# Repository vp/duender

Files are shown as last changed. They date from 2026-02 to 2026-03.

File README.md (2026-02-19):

<!-- Improved compatibility of back to top link: See: https://github.com/othneildrew/Best-README-Template/pull/73 -->

<!--
*** Thanks for checking out the Best-README-Template. If you have a suggestion
*** that would make this better, please fork the repo and create a pull request
*** or simply open an issue with the tag "enhancement".
*** Don't forget to give the project a star!
*** Thanks again! Now go create something AMAZING! :D
-->

<!-- PROJECT SHIELDS -->
<!--
*** I'm using markdown "reference style" links for readability.
*** Reference links are enclosed in brackets [ ] instead of parentheses ( ).
*** See the bottom of this document for the declaration of the reference variables
*** for contributors-url, forks-url, etc. This is an optional, concise syntax you may use.
*** https://www.markdownguide.org/basic-syntax/#reference-style-links
-->
<!--
[![Contributors][contributors-shield]][contributors-url]
[![Forks][forks-shield]][forks-url]
[![Stargazers][stars-shield]][stars-url]
[![Issues][issues-shield]][issues-url]
[![Unlicense License][license-shield]][license-url]
[![LinkedIn][linkedin-shield]][linkedin-url]
-->

<!-- PROJECT LOGO -->
<br />
<div align="center">
  <a href="https://www.printables.com/model/1300968-duender-mgn9h-2x-creality-ender-3-corexy-convertio">
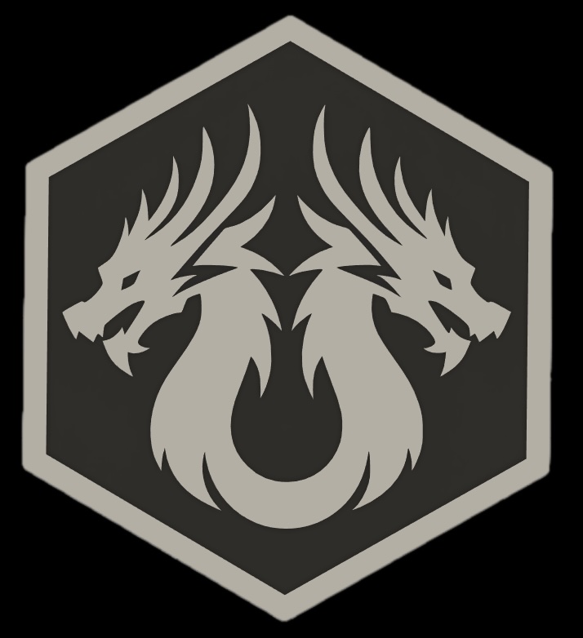
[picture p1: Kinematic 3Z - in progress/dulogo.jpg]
    
  </a>

  <h3 align="center">Duender mods, triple Z and more...</h3>
  <p align="center">
    Some thougths and mods for the duender project here.
    <br />Note: this is NOT an official repo, Irbis3D repo is <a href="https://github.com/Irbis3D">HERE</a>. Thanks.
  </p>
  <p>
    The Duender project is created and developped by Irbis3D <a href="https://discord.com/channels/1341676245171048473/1354698746524598312">Discord server</a>
  </p>
    <!--
    <br />
    <br />
    <a href="https://github.com/tallothendill/duender/tree/71d104ec3dbbbacea63be96e859a8f34e3e835fc/Kinematic%203Z%20-%20in%20progress">Triple Z axis, with kinematic bed</a>
    </p>X
    &middot;
    <a href="https://github.com/tallothendill/duender/tree/c5b984b065c5a199969d3fe1e7d17b98502cc63b/mods">Mods & stl related to the duender manual</a>
    &middot;
    <a href="https://github.com/othneildrew/Best-README-Template/issues/new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">Request Feature</a>
  </p>
</div>
-->

<!-- TABLE OF CONTENTS -->

<!--
<details>
  <summary>Table of Contents</summary>
  <ol>
    <li>
      <a href="#about-the-project">About The Project</a>
      <ul>
        <li><a href="#built-with">Built With</a></li>
      </ul>
    </li>
    <li>
      <a href="#getting-started">Getting Started</a>
      <ul>
        <li><a href="#prerequisites">Prerequisites</a></li>
        <li><a href="#installation">Installation</a></li>
      </ul>
    </li>
    <li><a href="#usage">Usage</a></li>
    <li><a href="#roadmap">Roadmap</a></li>
    <li><a href="#contributing">Contributing</a></li>
    <li><a href="#license">License</a></li>
    <li><a href="#contact">Contact</a></li>
    <li><a href="#acknowledgments">Acknowledgments</a></li>
  </ol>
</details>
-->

<!-- ABOUT THE PROJECT -->
<!--
## About The Project

[![Product Name Screen Shot][product-screenshot]](https://example.com)

There are many great README templates available on GitHub; however, I didn't find one that really suited my needs so I created this enhanced one. I want to create a README template so amazing that it'll be the last one you ever need -- I think this is it.

Here's why:
* Your time should be focused on creating something amazing. A project that solves a problem and helps others
* You shouldn't be doing the same tasks over and over like creating a README from scratch
* You should implement DRY principles to the rest of your life :smile:

Of course, no one template will serve all projects since your needs may be different. So I'll be adding more in the near future. You may also suggest changes by forking this repo and creating a pull request or opening an issue. Thanks to all the people have contributed to expanding this template!

Use the `BLANK_README.md` to get started.

<p align="right">(<a href="#readme-top">back to top</a>)</p>

### Built With

This section should list any major frameworks/libraries used to bootstrap your project. Leave any add-ons/plugins for the acknowledgements section. Here are a few examples.

* [![Next][Next.js]][Next-url]
* [![React][React.js]][React-url]
* [![Vue][Vue.js]][Vue-url]
* [![Angular][Angular.io]][Angular-url]
* [![Svelte][Svelte.dev]][Svelte-url]
* [![Laravel][Laravel.com]][Laravel-url]
* [![Bootstrap][Bootstrap.com]][Bootstrap-url]
* [![JQuery][JQuery.com]][JQuery-url]

<p align="right">(<a href="#readme-top">back to top</a>)</p>
-->

<!-- GETTING STARTED -->
<!--
## Getting Started

This is an example of how you may give instructions on setting up your project locally.
To get a local copy up and running follow these simple example steps.

### Prerequisites

This is an example of how to list things you need to use the software and how to install them.
* npm
  ```sh
  npm install npm@latest -g
  ```

### Installation

_Below is an example of how you can instruct your audience on installing and setting up your app. This template doesn't rely on any external dependencies or services._

1. Get a free API Key at [https://example.com](https://example.com)
2. Clone the repo
   ```sh
   git clone https://github.com/github_username/repo_name.git
   ```
3. Install NPM packages
   ```sh
   npm install
   ```
4. Enter your API in `config.js`
   ```js
   const API_KEY = 'ENTER YOUR API';
   ```
5. Change git remote url to avoid accidental pushes to base project
   ```sh
   git remote set-url origin github_username/repo_name
   git remote -v # confirm the changes
   ```

<p align="right">(<a href="#readme-top">back to top</a>)</p>
-->

<!-- USAGE EXAMPLES -->
<!--
## Usage

Use this space to show useful examples of how a project can be used. Additional screenshots, code examples and demos work well in this space. You may also link to more resources.

_For more examples, please refer to the [Documentation](https://example.com)_

<p align="right">(<a href="#readme-top">back to top</a>)</p>
-->

<!-- ROADMAP -->
<!--
## Roadmap

- [x] Add Changelog
- [x] Add back to top links
- [ ] Add Additional Templates w/ Examples
- [ ] Add "components" document to easily copy & paste sections of the readme
- [ ] Multi-language Support
    - [ ] Chinese
    - [ ] Spanish

See the [open issues](https://github.com/othneildrew/Best-README-Template/issues) for a full list of proposed features (and known issues).

<p align="right">(<a href="#readme-top">back to top</a>)</p>
-->

<!-- CONTRIBUTING -->
<!--
## Contributing

Contributions are what make the open source community such an amazing place to learn, inspire, and create. Any contributions you make are **greatly appreciated**.

If you have a suggestion that would make this better, please fork the repo and create a pull request. You can also simply open an issue with the tag "enhancement".
Don't forget to give the project a star! Thanks again!

1. Fork the Project
2. Create your Feature Branch (`git checkout -b feature/AmazingFeature`)
3. Commit your Changes (`git commit -m 'Add some AmazingFeature'`)
4. Push to the Branch (`git push origin feature/AmazingFeature`)
5. Open a Pull Request

### Top contributors:

<a href="https://github.com/othneildrew/Best-README-Template/graphs/contributors">
  <img src="https://contrib.rocks/image?repo=othneildrew/Best-README-Template" alt="contrib.rocks image" />
</a>

<p align="right">(<a href="#readme-top">back to top</a>)</p>
-->

<!-- LICENSE -->
<!--
## License

Distributed under the Unlicense License. See `LICENSE.txt` for more information.

<p align="right">(<a href="#readme-top">back to top</a>)</p>
-->

<!-- CONTACT -->
<!--
## Contact

Your Name - [@your_twitter](https://twitter.com/your_username) - email@example.com

Project Link: [https://github.com/your_username/repo_name](https://github.com/your_username/repo_name)

<p align="right">(<a href="#readme-top">back to top</a>)</p>
-->

<!-- ACKNOWLEDGMENTS -->
<!--
## Acknowledgments

Use this space to list resources you find helpful and would like to give credit to. I've included a few of my favorites to kick things off!

* [Choose an Open Source License](https://choosealicense.com)
* [GitHub Emoji Cheat Sheet](https://www.webpagefx.com/tools/emoji-cheat-sheet)
* [Malven's Flexbox Cheatsheet](https://flexbox.malven.co/)
* [Malven's Grid Cheatsheet](https://grid.malven.co/)
* [Img Shields](https://shields.io)
* [GitHub Pages](https://pages.github.com)
* [Font Awesome](https://fontawesome.com)
* [React Icons](https://react-icons.github.io/react-icons/search)

<p align="right">(<a href="#readme-top">back to top</a>)</p>
-->

<!-- MARKDOWN LINKS & IMAGES -->
<!-- https://www.markdownguide.org/basic-syntax/#reference-style-links -->
<!--
[contributors-shield]: https://img.shields.io/github/contributors/othneildrew/Best-README-Template.svg?style=for-the-badge
[contributors-url]: https://github.com/othneildrew/Best-README-Template/graphs/contributors
[forks-shield]: https://img.shields.io/github/forks/othneildrew/Best-README-Template.svg?style=for-the-badge
[forks-url]: https://github.com/othneildrew/Best-README-Template/network/members
[stars-shield]: https://img.shields.io/github/stars/othneildrew/Best-README-Template.svg?style=for-the-badge
[stars-url]: https://github.com/othneildrew/Best-README-Template/stargazers
[issues-shield]: https://img.shields.io/github/issues/othneildrew/Best-README-Template.svg?style=for-the-badge
[issues-url]: https://github.com/othneildrew/Best-README-Template/issues
[license-shield]: https://img.shields.io/github/license/othneildrew/Best-README-Template.svg?style=for-the-badge
[license-url]: https://github.com/othneildrew/Best-README-Template/blob/master/LICENSE.txt
[linkedin-shield]: https://img.shields.io/badge/-LinkedIn-black.svg?style=for-the-badge&logo=linkedin&colorB=555
[linkedin-url]: https://linkedin.com/in/othneildrew
[product-screenshot]: images/screenshot.png
[Next.js]: https://img.shields.io/badge/next.js-000000?style=for-the-badge&logo=nextdotjs&logoColor=white
[Next-url]: https://nextjs.org/
[React.js]: https://img.shields.io/badge/React-20232A?style=for-the-badge&logo=react&logoColor=61DAFB
[React-url]: https://reactjs.org/
[Vue.js]: https://img.shields.io/badge/Vue.js-35495E?style=for-the-badge&logo=vuedotjs&logoColor=4FC08D
[Vue-url]: https://vuejs.org/
[Angular.io]: https://img.shields.io/badge/Angular-DD0031?style=for-the-badge&logo=angular&logoColor=white
[Angular-url]: https://angular.io/
[Svelte.dev]: https://img.shields.io/badge/Svelte-4A4A55?style=for-the-badge&logo=svelte&logoColor=FF3E00
[Svelte-url]: https://svelte.dev/
[Laravel.com]: https://img.shields.io/badge/Laravel-FF2D20?style=for-the-badge&logo=laravel&logoColor=white
[Laravel-url]: https://laravel.com
[Bootstrap.com]: https://img.shields.io/badge/Bootstrap-563D7C?style=for-the-badge&logo=bootstrap&logoColor=white
[Bootstrap-url]: https://getbootstrap.com
[JQuery.com]: https://img.shields.io/badge/jQuery-0769AD?style=for-the-badge&logo=jquery&logoColor=white
[JQuery-url]: https://jquery.com 
-->

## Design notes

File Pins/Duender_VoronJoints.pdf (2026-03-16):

## Blind joints “a la Voron“ ADDON ⁻ All versions

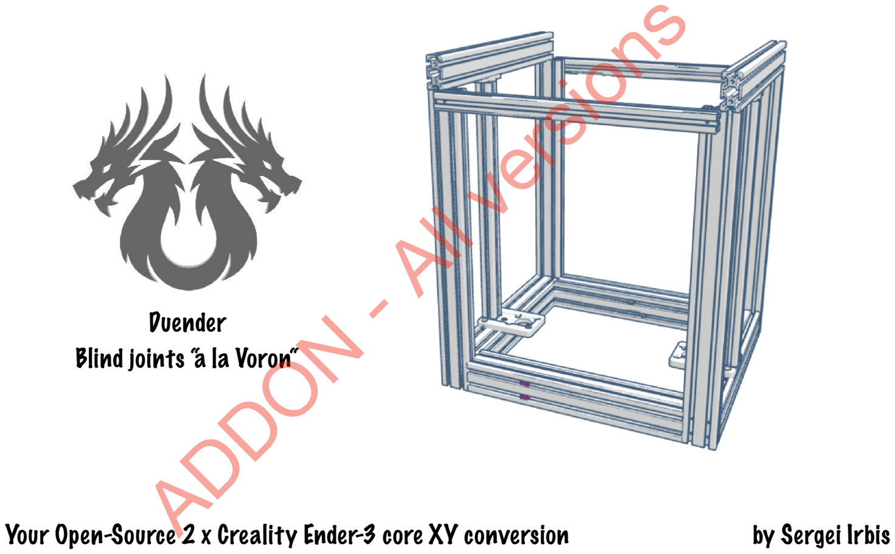
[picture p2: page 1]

## Duender

Your Open-Source 2 x Creality Ender-3 core XY conversion | by Sergei Irbis

## Caution!

For this method to work, your extrusions cuts must be perfectly square with their body.
If the cut is not 90°, the assembly can not end square!
You can somewhat compensate with a shim where needed, but this solution has its limits, plus it may create unwanted gaps between your extrusions.

two printed parts to help with the process:

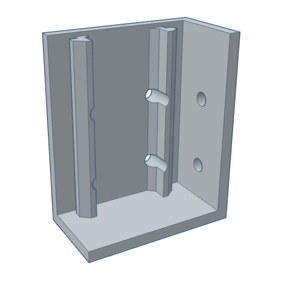
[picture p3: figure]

A simple drilling jig, to place the holes without too much thinking.
Many models exist online, some even with bearings to guide you.

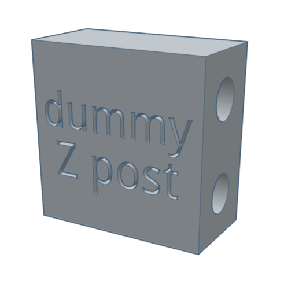
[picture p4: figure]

A 40x40x20mm dummy to fill the space of 2040 vertical extrusions.
Its holes allow for two M5x45 SHCS Ender 3 screws to secure it onto 4040 extrusions sides.

TOOLS YOU’LL NEDD:

2mm Allen key

A drill, I went with a 4,2mm bit, but if you are precise enough, 4mm should be fine.
Note that a drill press will make things way easier, as it is important to drill straight and square into the extrusions.

A M5 tap, along with its handle, and some lubricant to cut the treads into the extrusions channels.

Base structure | 6

## Assembling the frame

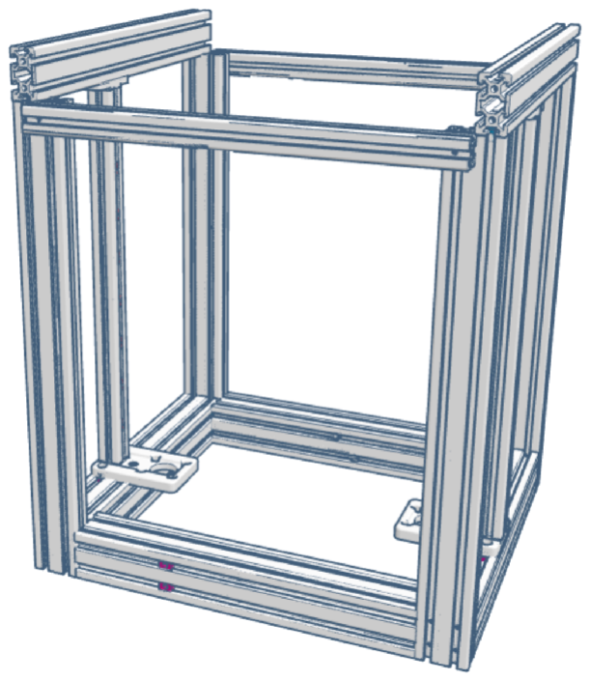
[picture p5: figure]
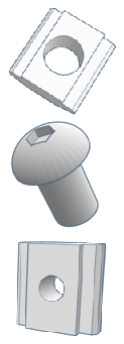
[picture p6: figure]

M5 T-slot nut | 18
M5x8 BHCS screw | 54
M3 T-slot nut | 16

Base structure | 7

2020-D *

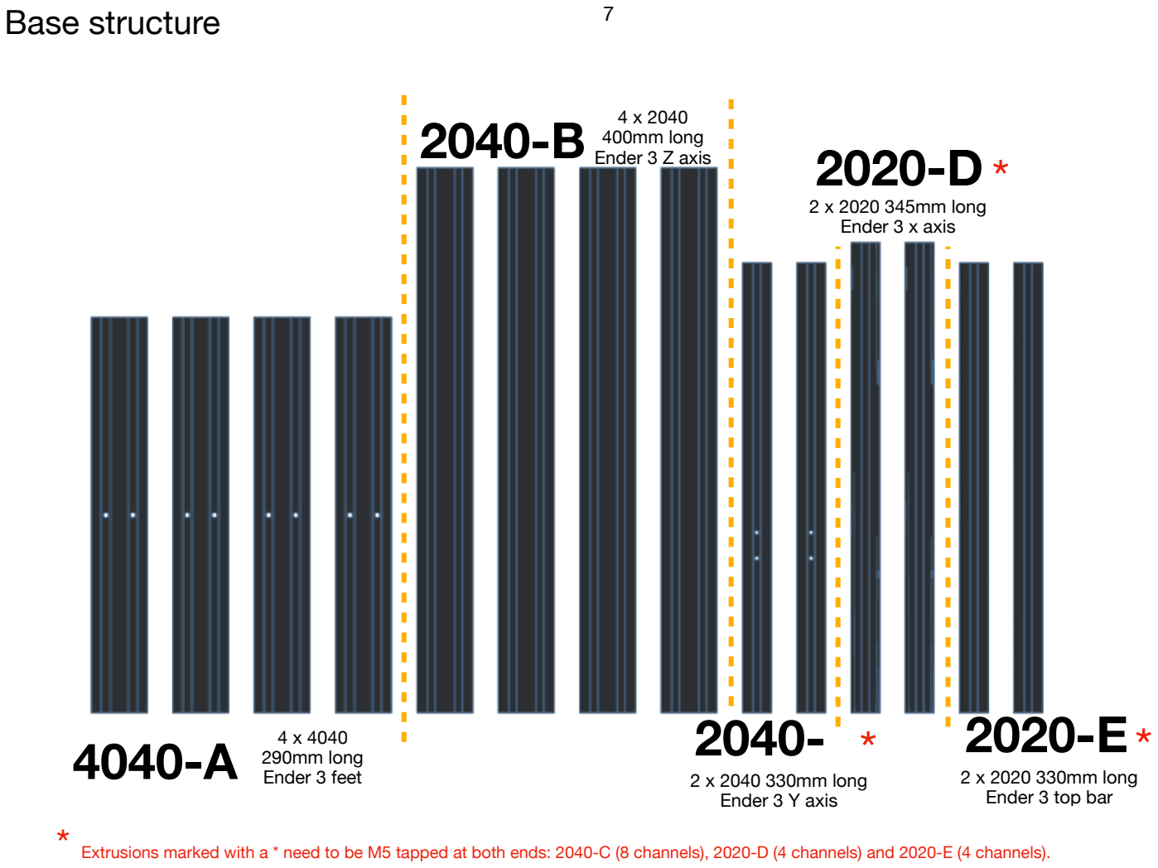
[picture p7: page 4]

4 x 2040
400mm long 2040-B Ender 3 Z axis

4 x 4040
290mm long 4040-A Ender 3 feet | 2 x 2040 330mm long
| Ender 3 Y axis

2040- *

2 x 2020 345mm long
Ender 3 x axis

2 x 2020 330mm long
Ender 3 top bar

2020-E*

* Extrusions marked with a * need to be M5 tapped at both ends: 2040-C (8 channels), 2020-D (4 channels) and 2020-E (4 channels).

Base structure | 8

Drill the 400mm 2040 Z posts bases
2 holes in the 20mm side, 4 holes in the 40mm face.

Bottom holes have their centre at 10mm from the base, Top holes are centred at 30mm from the base.

Of course, all are centred in the middle of the rails.
Be precise when marking or centre-punching those.

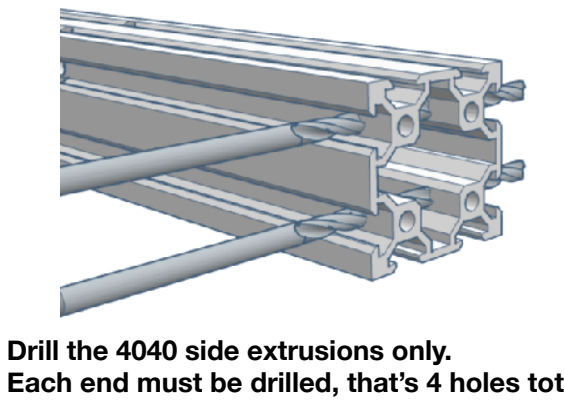
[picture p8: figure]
Drill the 4040 side extrusions only.

Each end must be drilled, that’s 4 holes total.

The front and back 4040 remain untouched.

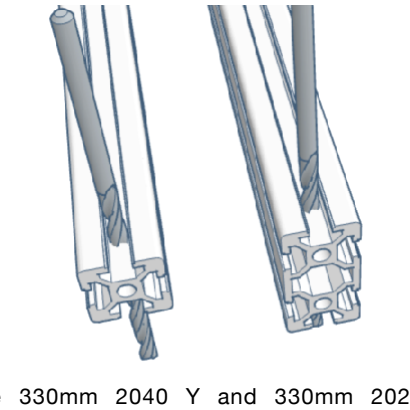
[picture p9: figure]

Same dimensions and requirements here. | The 330mm 2040 Y and 330mm 2020-E
| extrusions only need one hole on each end
| (10mm from the end).

Base structure | 9

Tap all the 4040 extrusions channels with a M5 bit. 4 extrusions, 4 holes on each side, that’s 32 holes to cut threads into.
You will also need to tap the 400mm 2040 channels (16 total), the 330mm 2040 channels (8 more), the 345mm 2020 extrusions (4), and one of the 330mm 2020 (only 2 here). Yes, that’s a lot.

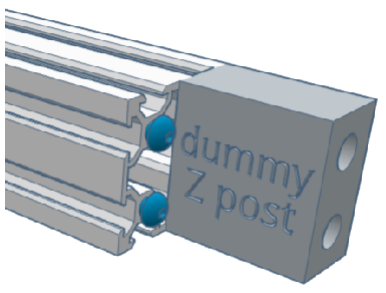
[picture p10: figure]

Use the dummy Z post, with two M5x45 screws from the ender 3 frame, and attach it in the front side of the front 4040 extrusion.
Two M5x8 BHCS are inserted in the inner most channels, nearly all the way in.

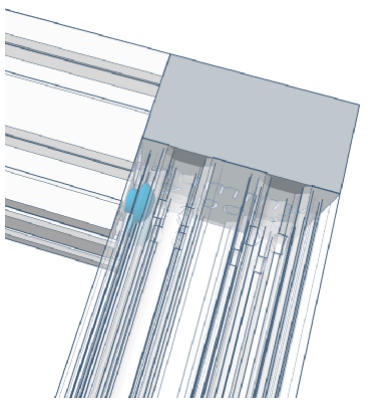
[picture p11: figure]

The dummy serves as a stop when sliding the side 4040 onto the BHCS heads.

Press the 4040 as far and flush as possible.

Base structure | 10

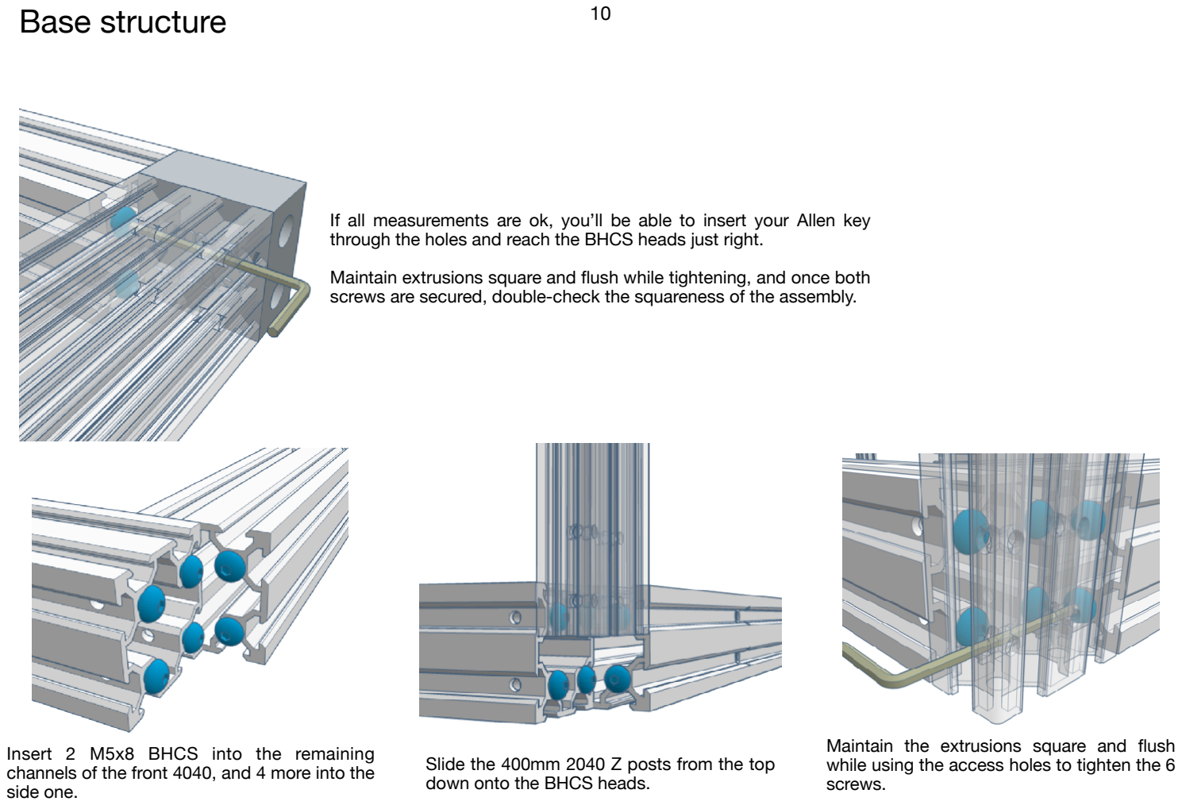
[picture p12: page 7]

If all measurements are ok, you’ll be able to insert your Allen key through the holes and reach the BHCS heads just right.

Maintain extrusions square and flush while tightening, and once both screws are secured, double-check the squareness of the assembly.

Insert 2 M5x8 BHCS into the remaining channels of the front 4040, and 4 more into the side one.

Slide the 400mm 2040 Z posts from the top down onto the BHCS heads.

Maintain the extrusions square and flush while using the access holes to tighten the 6 screws.

Base structure | 11

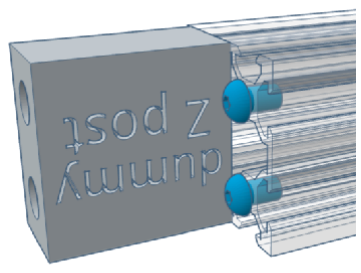
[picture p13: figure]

Continue by screwing the dummy on the
opposite side of the 4040 front extrusion, and

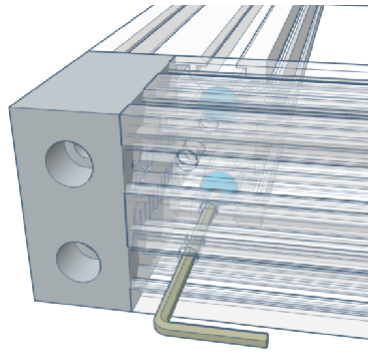
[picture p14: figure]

inserting 2 M5x8 BHCS in the inside channels | Insert the side 4040 to press against the dummy,
| and proceed with tightening the screws once
| you are all flat and flush.

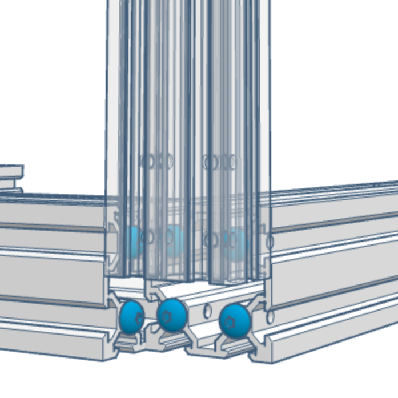
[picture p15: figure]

Same as before, insert 6 M5x8 BHCS in the channels once you got the dummy out, insert the front right 2040 by the top and proceed to squaring and assembly

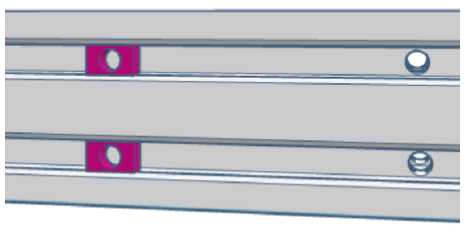
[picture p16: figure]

Slide 2 M5 T-slot nuts in the front channels as pictured

Slide 2 M5 T-slot nuts in the outer top channel and 1 M5 T-slot nut in the inner one of both side extrusion as pictured
(6 M5 T-slot nuts total)

Base structure | 12

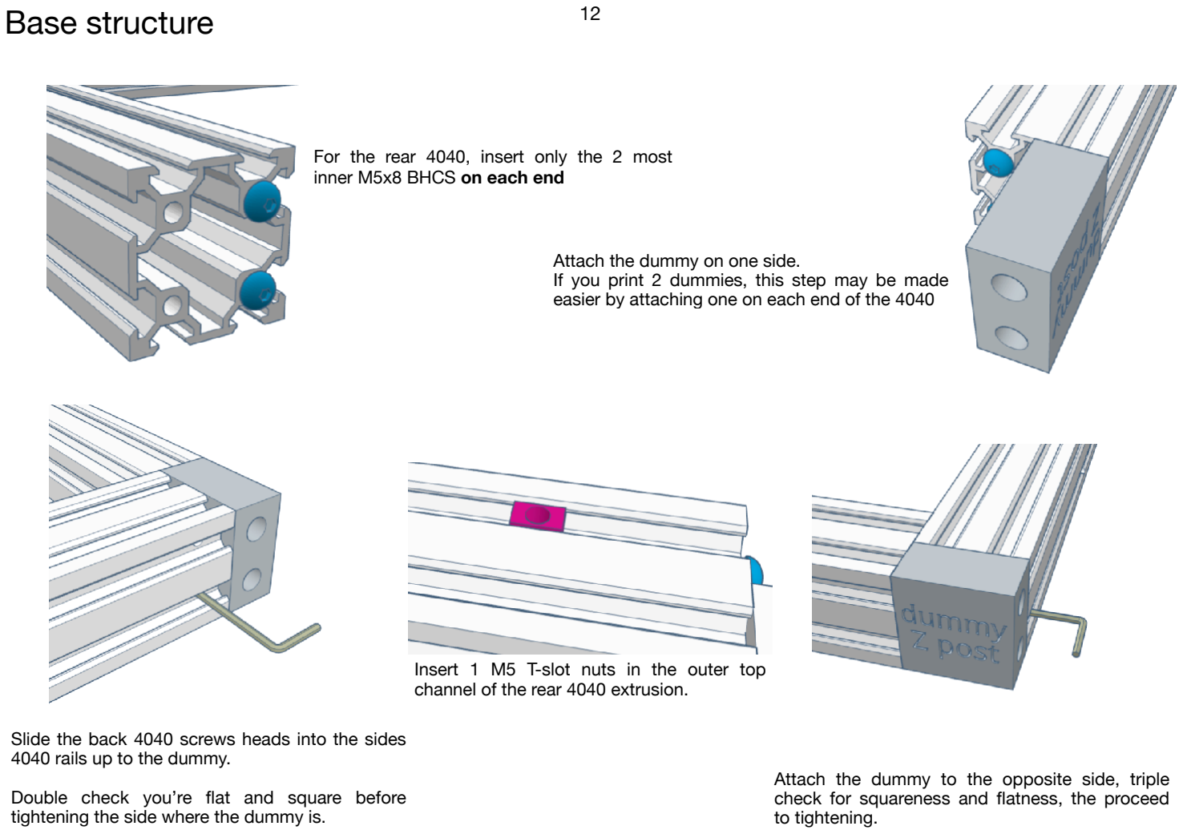
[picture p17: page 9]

For the rear 4040, insert only the 2 most inner M5x8 BHCS on each end

Attach the dummy on one side.
If you print 2 dummies, this step may be made easier by attaching one on each end of the 4040

Slide the back 4040 screws heads into the sides 4040 rails up to the dummy.

Double check you’re flat and square before tightening the side where the dummy is.

Attach the dummy to the opposite side, triple check for squareness and flatness, the proceed to tightening.

Insert 1 M5 T-slot nuts in the outer top channel of the rear 4040 extrusion.

Base structure | 13

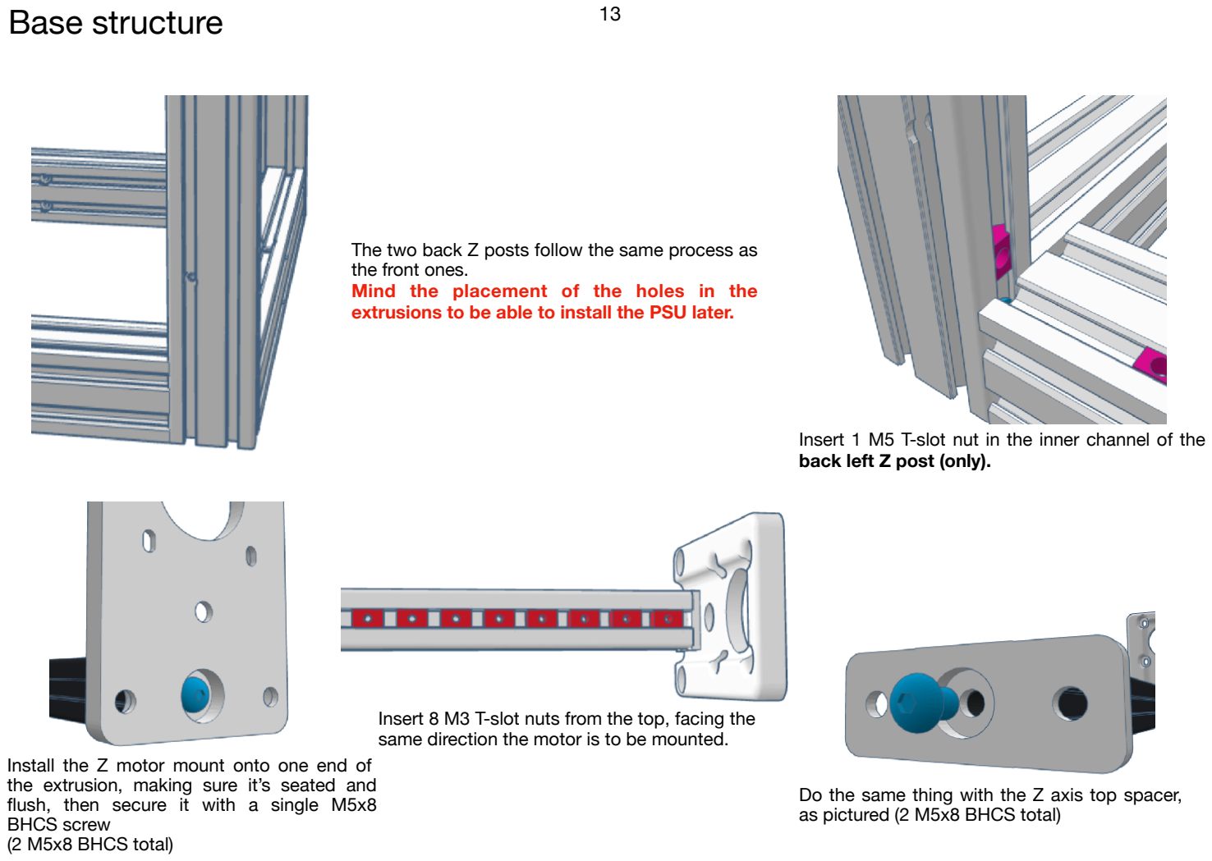
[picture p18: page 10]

The two back Z posts follow the same process as the front ones.
Mind the placement of the holes in the extrusions to be able to install the PSU later.

Insert 1 M5 T-slot nut in the inner channel of the back left Z post (only).

Install the Z motor mount onto one end of the extrusion, making sure it’s seated and flush, then secure it with a single M5x8 BHCS screw
(2 M5x8 BHCS total)

Do the same thing with the Z axis top spacer, as pictured (2 M5x8 BHCS total)

Insert 8 M3 T-slot nuts from the top, facing the same direction the motor is to be mounted.

Base structure | 14

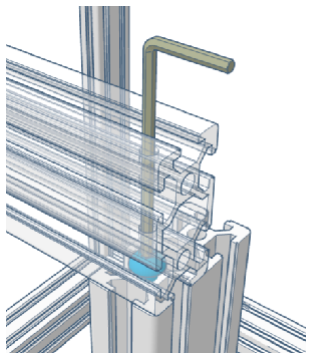
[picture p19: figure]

You should the be able to slide the 330mm 2040 Y extrusions onto the screws heads, and once sure they are flush, tighten them in.

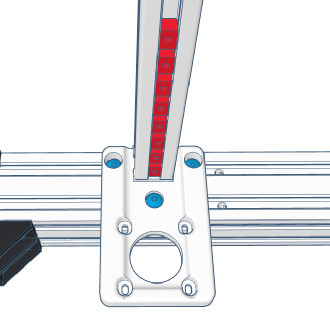
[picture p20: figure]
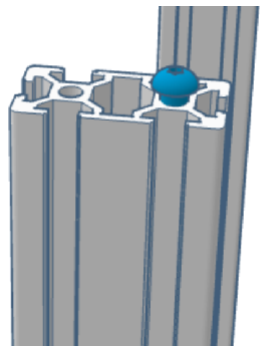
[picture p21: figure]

Once your Z axis are sorted, place 1 M5x8 BHCS on top of the outer channel of each 400mm Z post.

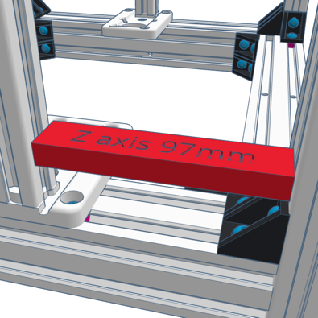
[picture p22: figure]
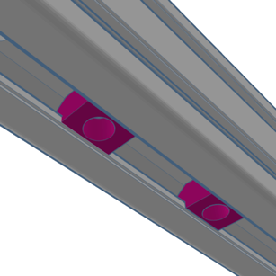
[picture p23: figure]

Slide 2 M5 T-slot nuts on the underside of each 330mm 2040 Y axis
(4 M5 T-slot nuts total)

Install the Z axis onto one side of the base
Align the previously installed M5 T-slot nuts with the holes Secure it with three M5x8 BHCS screws
(6 M5x8 BHCS total)
DO NOT FULLY TIGHTEN THE SCREWS YET The axis needs to be able to slide side to side

Use the 3D printed spacer provided in the tools
OR a calliper to adjust the Z axis 97mm from the front post, then tighten the 3 M5x8 BHCS screws of the base
This is the default distance. You may need to adjust this distance later, depending on your toolhead configuration

Base structure | 15

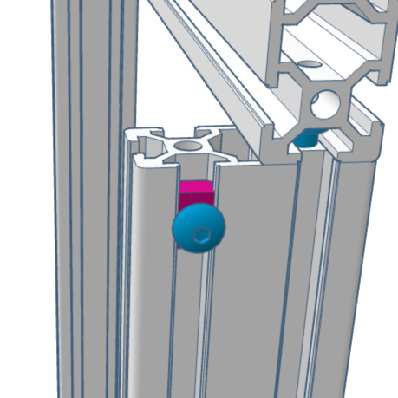
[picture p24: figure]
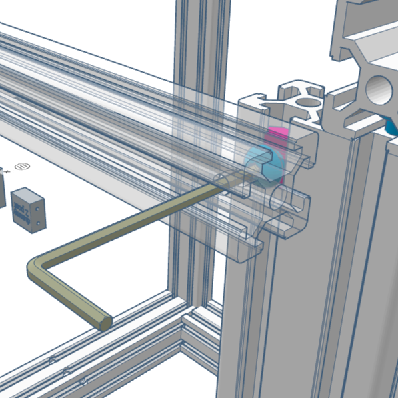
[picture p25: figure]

Slide a M5 BHCS+M5 T-slot nut assembly
into the outer rail of each back 400mm 2040 Z post

You can now use the access hole into the 330mm 2020-E back brace to secure it to the back of the frame.
Make sure it’s level flat and centred.

Repeat those last 2 steps for the front brace.

One last check at every angle and corner that everything is square, straight, flush, level, you name it, and you’re good to go.

Align the 2 M5 T-slot nuts remaining under the 2040-C with the top Z axis plate, and use 2 M5x8 BHCS screws to secure it

Check the distance to the front post to be 97mm all along the Z axis before tightening the screws

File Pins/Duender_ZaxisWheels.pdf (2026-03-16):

## V-wheels Z axis ADDON ⁻ “Pins” version


## Duender

Your Open-Source 2 x Creality Ender-3 core XY conversion | by Sergei Irbis

Assembling the Z axis | 16

## Z gantry

Wheel M5 spacer; (from Ender 3); M5 Nylstop nut; Eccentric M5 nut; M5x30 BHCS screw; M4x35 FHCS; M4 Nylstop nut; Open Build plates; M3 Nylstop nut; 12mm silicone spacers; Nema 17 42-34; M3x16 BHCS screw; (from Ender 3) 4; M3x8 BHCS screw

Lead screw nut | 2
(from Ender 3)
8mm lead screw | 2
(from Ender 3)
POM V-Wheel | 8
(from Ender 3)
Motor shaft coupler | 2
(from Ender 3)

Assembling the Z axis | 17

Insert 4 M5x30 BHCS from the underside Spacers go over the smaller holes and

Install the lead screw nuts under the plastic bed holders, and insert 2 M3x16 SHCS or BHCS screws (Or you can use the ones originally coming from your Ender 3)

If you lead screws aren’t perfectly straight, it is advised that you swap the original lead screw nuts from the Ender 3 with some anti-backlash ones, to avoid Z wobble

eccentric nuts over the larger ones
Those are all from the original Ender 3 rollers mounts

and an M5 Nylstop (self-locking) nut

Finally, add 4 V-rollers from your Ender 3,

DO NOT TIGHTEN THE NUTS YET, you need the whole screws/wheels to be loose


Turn the bed holders around being careful not to lose the screws and secure them with M3 nuts

Assembling the Z axis | 18


Place the rollers plate behind the bed holder and use 4 M3x8 BHCS screws to hold it Secure the screws with 4 M3 nuts


Place the Z motors under their plates and use 4 M3x8 BHCS screws to secure them. Orient the motor plug to the back of the printer


Install the lead screws couplers onto the Z motors shafts and tighten only the lower screw

If your lead screws aren’t perfectly straight, you may want to replace those with "spring" or "elastic" ones to avoid Z-wobble

Assembling the Z axis | 19


Insert the bed holder assembly onto the Z axis (note that the longer side goes towards the front) and tighten the V-wheels
Once secured, adjust the eccentric nuts to ensure all 4 wheels apply equal pressure


The wheels should rotate smoothly with a slight resistance when turned by hand

Double check that the screws heads don’t touch the extrusion surface.


Insert the lead screws into the lead screws nut from the top then insert them into the Z motor coupler by rotating them all the way down

Tighten the upper screw of the coupler to hold the lead screw

Assembling the Z axis | 20


Place the Ender 3 Y plate onto the bed holders, 4 silicone spacers -here 12mm shown in orange (you may use the springs from the Ender 3) then the heatbed
Of course, the wiring of the heatbed should end towards the back of your printer


Use the original 4 M4x35 FHCS screws and secure them under the bed holders with M4 nuts

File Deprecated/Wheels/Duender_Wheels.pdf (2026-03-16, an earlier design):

Your Open-Source 2 x Creality Ender-3 core XY conversion | by Sergei Irbis ADDON ⁻ “Mgn9h” version”

## Duender V-wheels AB & X axis

Building the AB kinematics | 22

## AB Gantry

M3x0,5 spacer; Nema 17 42-40; (from Ender 3); M3x30 SHCS; M3x8 SHCS; M3x16 SHCS; M3x20 SHCS
M5 T-slot nut; M3 Heat set insert; M3x10 spacer; M5x8 BHCS screw; GT216T6W3B toothless idler 8; GT216T6W5B motor pulley; M5 Nylstop nut; (from Ender 3); Wheel M5 spacer; POM V-Wheel; Eccentric M5 nut; M5x30 BHCS screw

Building the AB kinematics | 23


Prepare the bottom part of AB motor holders: with 6 M3 heat set inserts each side
(12 M3 heat set inserts total).


Install the motors under the plates with 2 M3x8 SHCS screws in the shown locations Mind the motor plug orientation

Also place the motor pulleys onto the shafts of A & B motors
Do not tighten them too much. They will need to be adjusted later, after belts installation


Pass 2 M3x30 SHCS into the idler holes and turn both top half upside down.

For the Left AB mount:

Stack 2 M3x0,5mm spacers, one GT2 16mm toothless idler, 2 M3x0,5mm spacers, the second idler, and 2 M3x0,5mm spacers onto the outer most pin (right side when upside down)
Stack 2 M3x0,5mm spacers, one GT2 16mm toothless idler, 2 more M3x0,5mm shims and a M3x10mm spacer on the inner-most pin.

The best option is certainly to buy and install a metal M3x10 spacer, but should you not have one on hand, you may use the printed one provided in the stl files.

Building the AB kinematics | 24


When the mounts are one against another, the idlers should be perfectly level between both sides. If that is not the case, adjust the shims count as necessary

For the Right AB mount:

Stack 2 M3x0,5mm spacers, one GT2 16mm toothless idler, 2 M3x0,5mm spacers, the second idler, and 2 M3x0,5mm spacers onto the outer most pin (left side when upside down).

Stack 3 M3x0,5mm spacers, one GT2 16mm toothless idler and 2 more M3x0,5mm spacers on the inner-most pin, onto the printed post


Put the parts on their back so shims don’t fall and assemble the two halves together.
Attach them adding 4 M3x30 SHCS on each side. (12 M3x30 SHCS total)

Building the AB kinematics | 25


Install the AB motor holders each side and use a M5x8 BHCS screw to secure it onto the top M5 T-slot nut


Use a second M5x8 BHCS screw to hold into the tapped end of the 2020-E back brace


Use a M5x8 BHCS screw to hold into the tapped end of the 2040-C Y axis and another one to hold onto the back brace M5 T-slot nut

Building the AB kinematics | 26


Install the motor holders with M3x16 SHCS that screws right into the motor

Secure the base of the holder with an M5x8 BHCS screw into one of the previously inserted T-slot nuts in front of the back brace


Prepare both carriage plates by inserting 4 M3 heat sets each side
(8 M3 heat inserts total).

Just like the Z plates, insert 3 M5x30 BHCS into each carriage, then on the outer side, 2 M5 spacers, the V-wheels, and M5 hex nuts to secure each stack.
In the inner side, stack the eccentric nut, 1 V-wheel and a M5 hex nut to tighten the whole. Leave them loose for now.

(6 M5x30 BHCS, 4 M5 spacers, 2 eccentric columns, 6 V-wheels and 6 M5 hex nuts total)


Place the carriages on both Y axis rails and tighten the M5 hex nuts, then proceed to adjusting the eccentric nut to adjust the pressure of the wheels.

Building the AB kinematics | 27

Install the front holders with 2 M5x8 BHCS screws each side

MIND THE SIDE, the holders are not symmetrical


Prepare both the Left and Right belt tensioners by placing an M3 heat set insert in the underside hole


Place 2 M3x0,5mm shims, a 16mm toothless idler and 2 M3x0,5mm shims, all held by a M3x20 SHCS screw inside each tensioner

As already mentioned, a printed jig (https://www.printables.com/model/1500832-duender-belt-tensioner-jig) can make this much easier


Insert an M5 Nylstop nut into the groove inside both holders. A light dab of glue may be used to ensure they stay in

Building the X axis | 28

## X axis gantry

M3x30 SHCS; M5 T-slot nut; M5x8 BHCS screw; M3 Heat set insert; M3x0,5 spacer; GT216T6W3B toothless idler 2; GT216T6W3B toothed idler; M3x6 SHCS; Modified toolhead plate; (from Ender 3)
Wheel M5 spacer; (from Ender 3); POM V-Wheel; Eccentric M5 nut; M5x30 BHCS screw; M5 Nylstop nut

Building the X axis | 29

Each half takes:
2 M3x0,5mm shims, a toothed idler and 3 M3x0,5mm shims on the front axis,

2 M3x0,5mm shims, a toothless idler and 3 M3x0,5mm shims on the rear one.

Turn both top halves upside down, and insert 2 M3x30 SHCS each side to serve as the idler axis

Prepare both bottom parts of the X carriage with 5 M3 heat set inserts each side.
Those in the printed posts are better inserted from below.

Place each bottom half onto its carriage, and secure it with 4 M3x6 SHCS
(8 M3x6 SHCS total).

Building the X axis | 30


Insert 2 M5 T-slot nuts on the top side, 2 on the back side and 2 more under the X axis extrusion
(6 M5 T-slot nuts total)

Push the X axis into its carriages on the two sides of the printer, carefully centre it then tighten both carriages.

Once done, use the previously inserted T-nuts to tighten 3 M5x8 BHCS at each end:
1 on top, 1 on the back and 1 under the X axis.
(6 M5x8 BHCS total)

Put the printer on its back so the shims don’t fall and tighten both axis, adding 3 M3x30 SHCS, to assemble the two halves.
( 6 M3x30 SHCS total)

Just screw enough so that parts hold together: both halves need to be lose for next step.

Place a M5x30 BHCS into the bottom of the toolhead plate, from below stack the eccentric nut, 1 V-wheel and tighten a M5 hex nut onto it.
Leave the nut loose for now.

Building the X axis | 31


Put the adapter plate onto the metal carriage, and attach it using 2 M5x30 BHCS that hold a M5 spacer, a V-wheel and a M5 hex nut from below.
Leave the nuts loose for now.

Pass the wheels around the X extrusion, the belts (installed in next section) will pass through the side openings and be folded ont themselves behind the metal plate. Attach its the ends onto itself with a zip tie.

Once everything is in place, tighten the M5 nuts to secure the wheels onto the extrusion, then proceed to the eccentric setting to adjust the wheels pressure.


Once assembled, the toolhead will be attached to the carriage using 2 M3x8 SHCS on the bottom, and 1 M3x18 SHCS on the top.

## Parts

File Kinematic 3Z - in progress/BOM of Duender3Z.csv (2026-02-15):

Item | Quantity | Description | Product line
1 | 2 | 4040-A 290mm extrusion | Ender 3 part
2 | 2 | 4040-A 290m extrusion | Ender 3 part
3 | 4 | 2040-B 400mm extrusion | Ender 3 part
4 | 2 | 2040-C 345mm extrusion | Ender 3 part
5 | 2 | 2020-E 345mm extrusion | Ender 3 part
6 | 5 | Nema 17 42-34 motor | Ender 3 part
7 | 3 | Motor coupler D5/8 | Ender 3 part
8 | 3 | T8 lead screw | Ender 3 part
9 | 1 | 235x235 Heat bed | Ender 3 part
10 | 2 | M5x25 SHCS | Ender 3 part
11 | 1 | 2040-C 345mm extrusion | Extrusion
12 | 1 | 2020-E 345mm extrusion | Extrusion
13 | 2 | 2020V 200mm | Extrusion
14 | 1 | 2020V 300mm | Extrusion
15 | 98 | M5x8 BHCS | Fastener
16 | 42 | M5 T-slot nut | Fastener
17 | 3 | M5x16 BHCS | Fastener
18 | 4 | M4x30 FHCS | Fastener
19 | 94 | M3x8 SHCS | Fastener
20 | 9 | M3x6 BHCS | Fastener
21 | 54 | M3 T-slot nut | Fastener
22 | 3 | TR8x8 leadscrew nut | Fastener
23 | 3 | GE5C bearing | Fastener
24 | 2 | M5 Hex nut | Fastener
25 | 4 | M3x8 BHCS | Fastener
26 | 2 | M3 Hammerhead nut | Fastener
27 | 18 | M3x5x4 Heat set insert | Fastener
28 | 6 | M3x35 SHCS | Fastener
29 | 14 | M3x30 SHCS | Fastener
30 | 8 | M3x6 SHCS | Fastener
31 | 4 | 12mm silicone spacer | Hardware
32 | 2 | M3x20mm pin | Hardware
33 | 6 | MGN9H 300mm rail | Kinematics
34 | 6 | MGN9H carriage | Kinematics
35 | 39 | M3x0.5mm shim | Kinematics
36 | 5 | M3x10mm spacer | Kinematics
37 | 8 | M3 pin | Kinematics
38 | 10 | 16T 6W 3B toothless idler | Kinematics
39 | 2 | GT2 16T 6W 5B pulley | Kinematics
40 | 2 | F695-2RS bearing | Kinematics
41 | 1 | GT2 6mm belt approx. 1.5m | Kinematics
42 | 1 | GT2 6mm belt approx. 1.5m | Kinematics
43 | 2 | 16T6W3B toothed idler | Kinematics
44 | 3 | Top Z spacer | Printed part
45 | 2 | Bottom Z spacer | Printed part
46 | 1 | PiTFT43 housing | Printed part
47 | 1 | Z motor holder back | Printed part
48 | 6 | Z Carriage stopper | Printed part
49 | 1 | Z joint back | Printed part
50 | 1 | Bed support back | Printed part
51 | 1 | Z joint left | Printed part
52 | 1 | Joint cover left | Printed part
53 | 2 | Z motor holder front | Printed part
54 | 1 | Bed support left | Printed part
55 | 1 | Z joint right | Printed part
56 | 1 | Joint cover right | Printed part
57 | 1 | Bed support right | Printed part
58 | 1 | AB motor mount BottomLeft | Printed part
59 | 1 | AB motor mount TopLeft | Printed part
60 | 2 | Y Carriage stopper | Printed part
61 | 1 | Front Left Holder Medusa9H | Printed part
62 | 1 | Left Tensioner Bottom | Printed part
63 | 1 | Left Tensioner Top | Printed part
64 | 1 | AB motor mount BottomRight | Printed part
65 | 1 | AB motor mount TopRight | Printed part
66 | 1 | Front Right Holder Medusa9H | Printed part
67 | 1 | Right Tensioner Bottom | Printed part
68 | 1 | Right Tensioner Top | Printed part
69 | 1 | Y Carriage Bottom Left | Printed part
70 | 1 | Y Carriage Bottom Right | Printed part
71 | 1 | Y Carriage Top Left | Printed part
72 | 1 | Y Carriage Top Right | Printed part

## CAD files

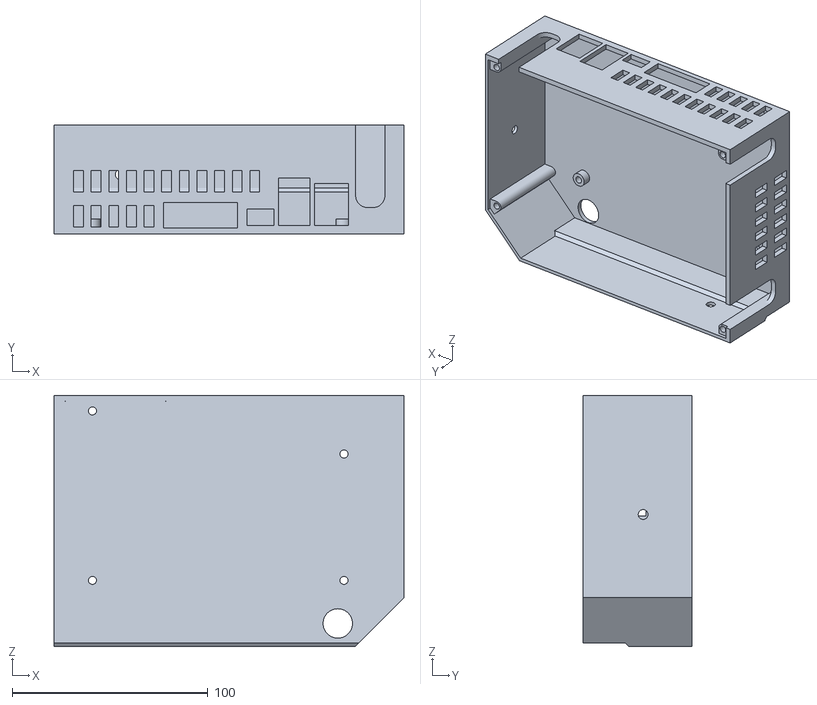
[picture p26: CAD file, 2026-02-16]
Pins/Electronics/Manta_Box_Main.stl
178.7 x 55.6 x 128.3

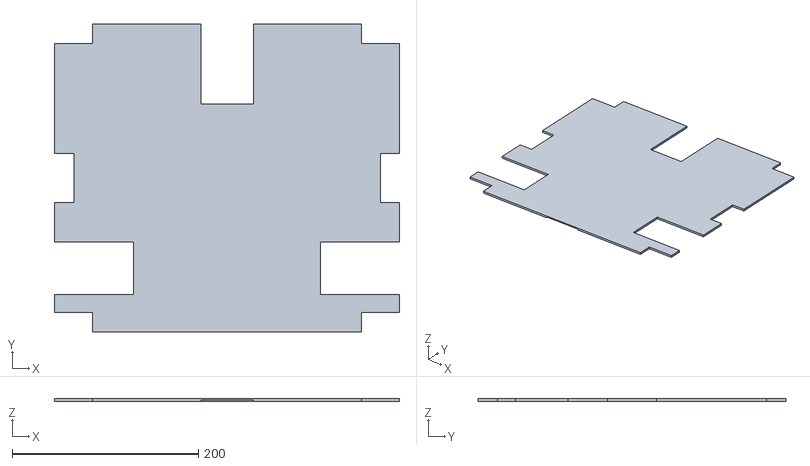
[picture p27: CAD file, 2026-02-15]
Kinematic 3Z - in progress/Base/Base_Lid.stl
370.0 x 330.0 x 3.00

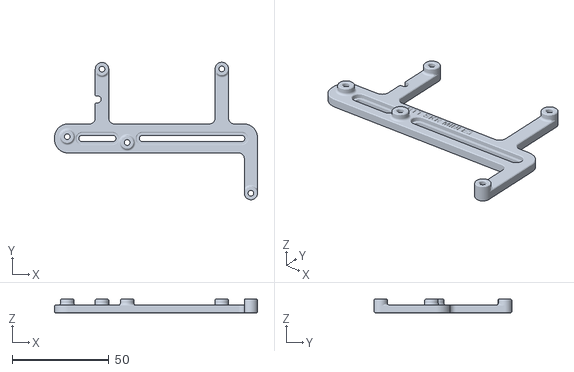
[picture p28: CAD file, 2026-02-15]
Kinematic 3Z - in progress/Base/EMS Mounts/FT - BTT SKR Mini E3 mount.stl
104.9 x 71.1 x 7.00

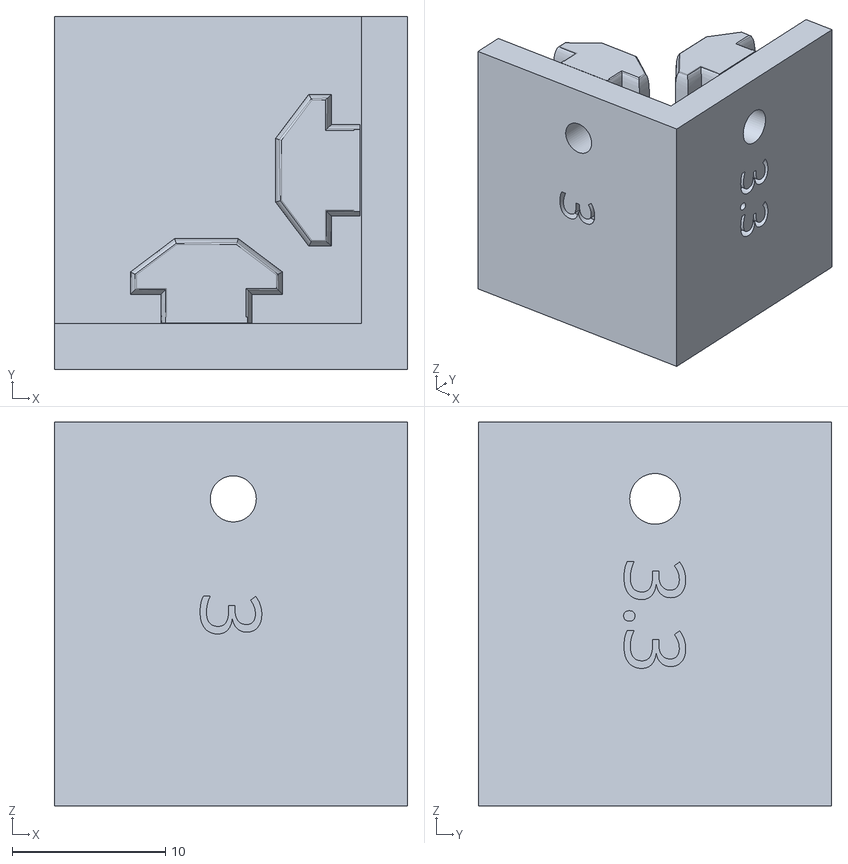
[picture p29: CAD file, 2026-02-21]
Kinematic 3Z - in progress/Extras/[t]_Bed_Mounts_Drill_Jig.stl
23.0 x 23.0 x 25.0

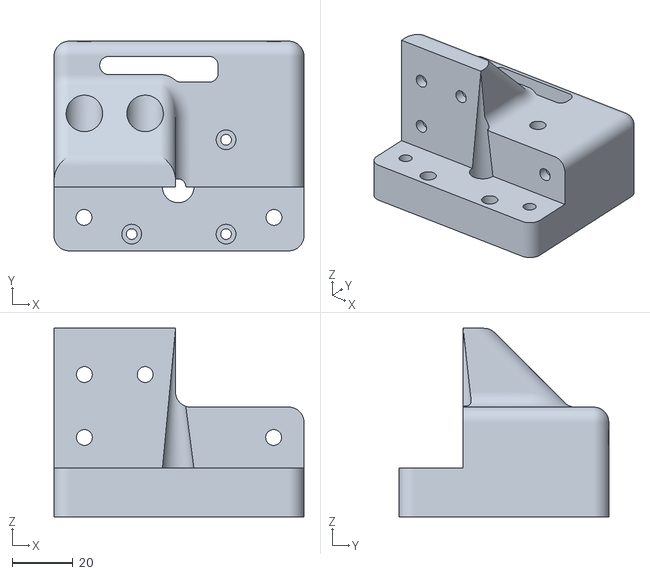
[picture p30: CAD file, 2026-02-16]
Kinematic 3Z - in progress/XY Axis/AB_Motor_Bottom_Right.stl
82.3 x 69.0 x 62.0

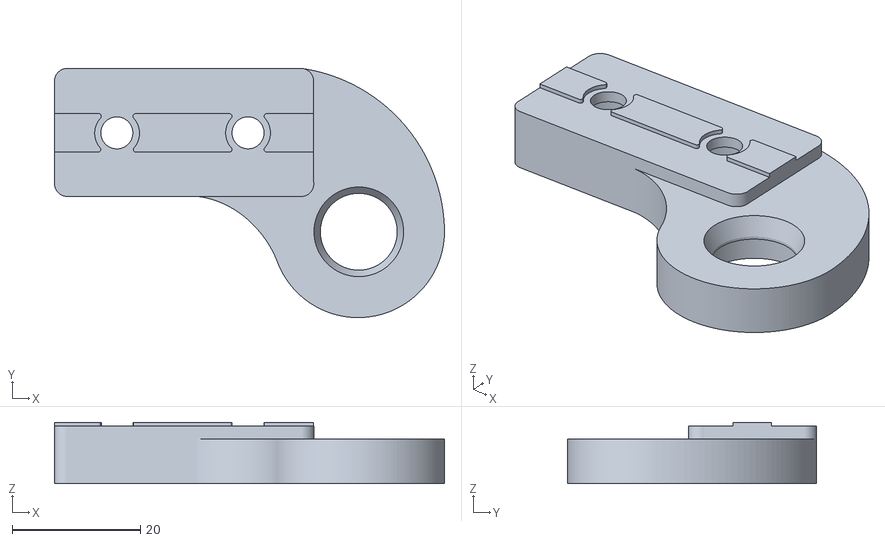
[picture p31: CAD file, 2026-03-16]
Kinematic 3Z - in progress/Z Axis/Bed_holder_Left.stl
60.9 x 38.9 x 9.60

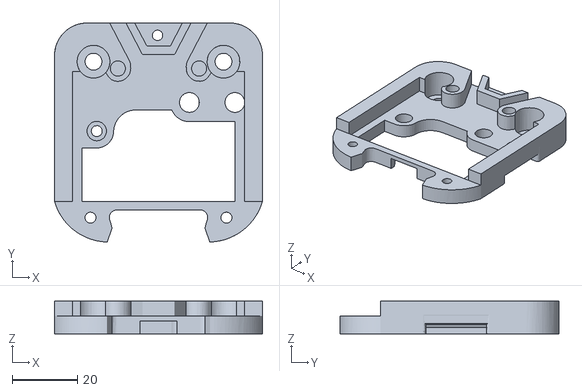
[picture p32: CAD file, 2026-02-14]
Mods/AdaptedAdapter_2mm.stl
64.0 x 67.4 x 10.0

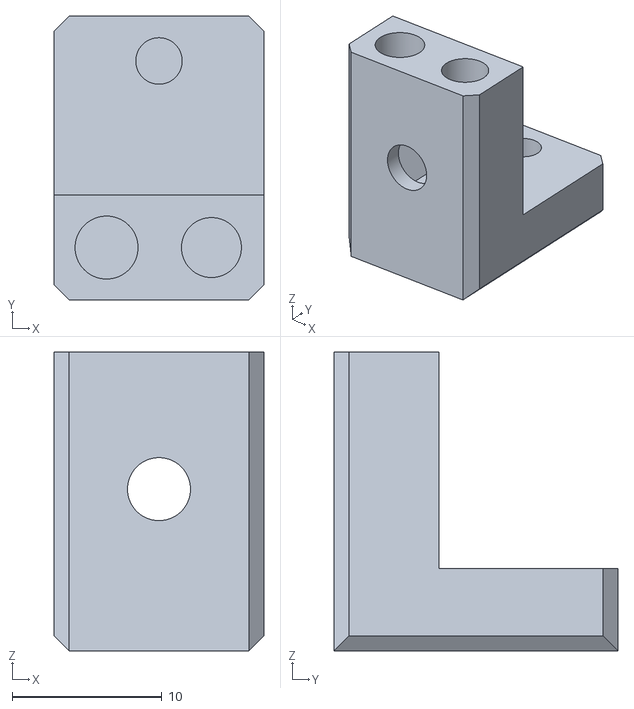
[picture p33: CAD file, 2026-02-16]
Pins/AB Axis/[9H]_Tensioner_Bottom_Left.stl
14.0 x 19.0 x 19.9

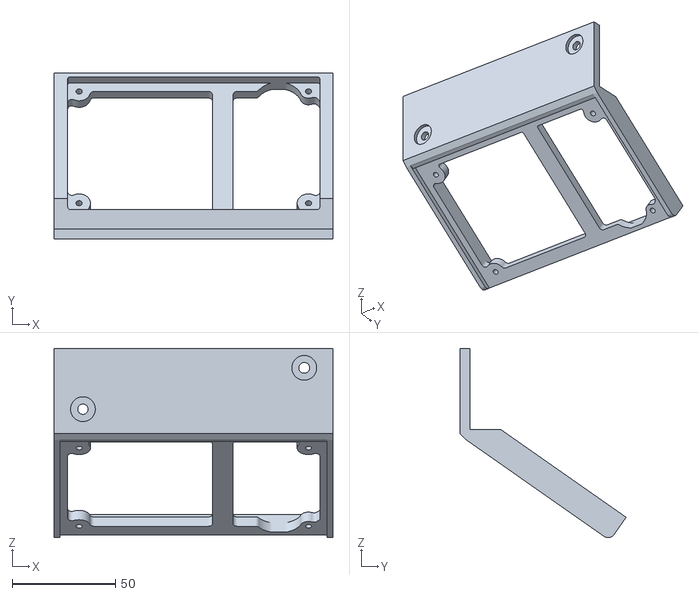
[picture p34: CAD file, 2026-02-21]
Pins/Electronics/HDMI5_Mount_noLogo.stl
135.0 x 80.5 x 91.6

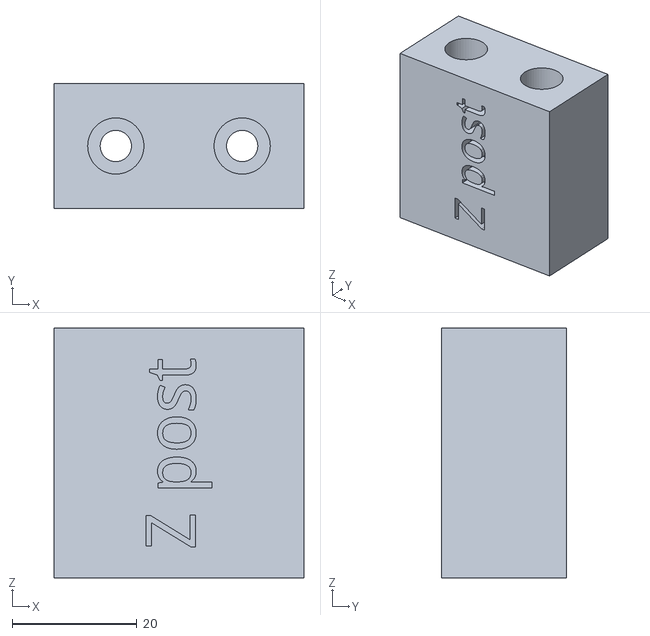
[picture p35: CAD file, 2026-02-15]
Pins/Extras/[t]_Zpost_Dummy_Jig.stl
40.0 x 20.0 x 40.0

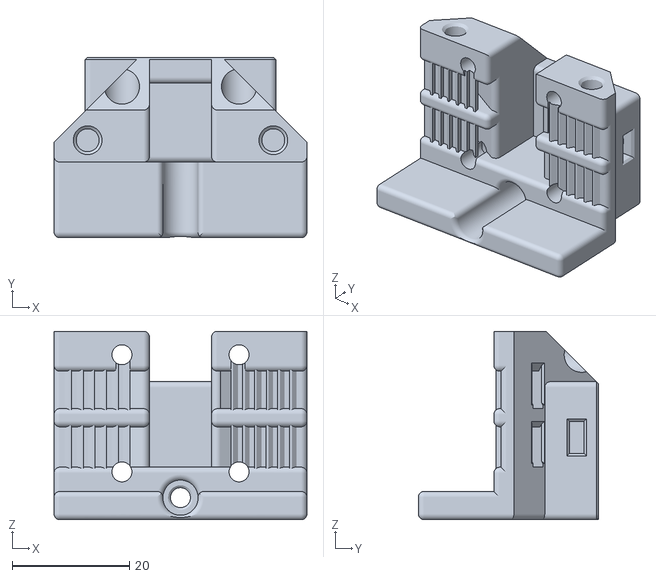
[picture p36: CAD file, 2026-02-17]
Pins/Toolhead/[12H]_Carriage_Mount.stl
43.2 x 30.8 x 32.2

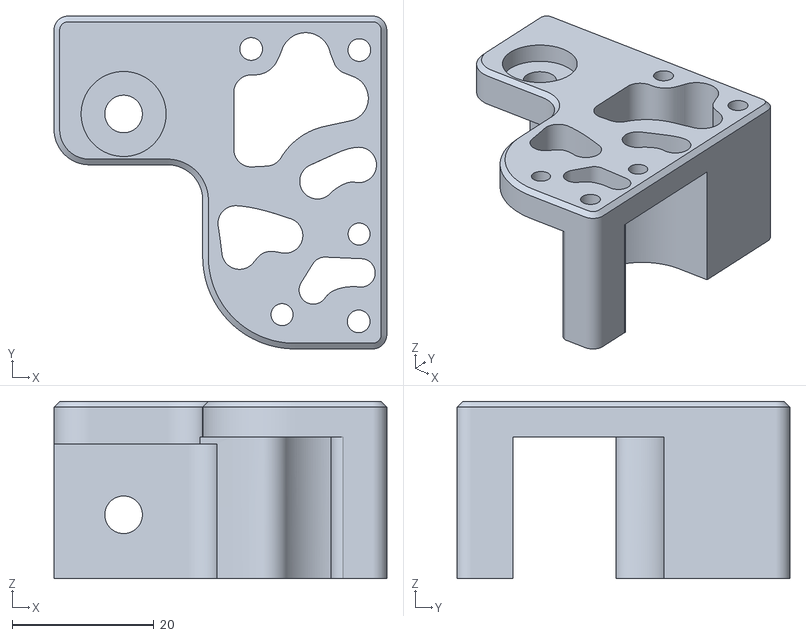
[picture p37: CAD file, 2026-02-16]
Pins/X Axis/[12H]_Y_Carriage_Top_Right.stl
47.0 x 47.0 x 25.0

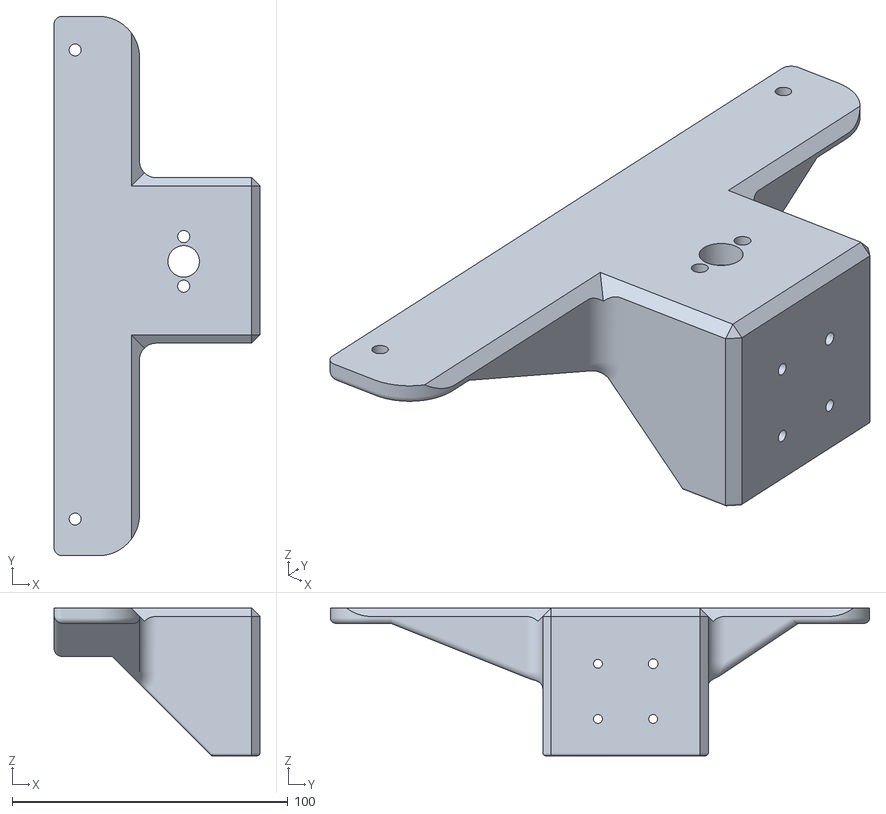
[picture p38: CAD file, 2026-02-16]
Pins/Z Axis/[12H]_Bed Hold R.stl
74.6 x 195.5 x 53.5

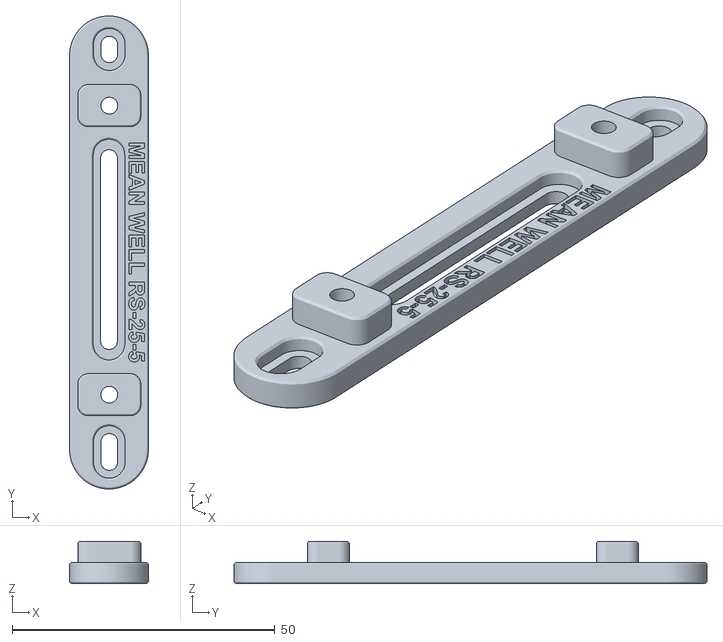
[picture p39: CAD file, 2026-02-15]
Kinematic 3Z - in progress/Base/EMS Mounts/FT - Mean Well RS-25-5 mount.stl
15.0 x 90.0 x 8.00

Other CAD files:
Kinematic 3Z - in progress/Base/Fan_Shrowd_x4.stl
Kinematic 3Z - in progress/Extras/2040_Half_Lid_x3.stl
Kinematic 3Z - in progress/XY Axis/AB_Motor_Bottom_Left.stl
Kinematic 3Z - in progress/Z Axis/Bed_holder_Back.stl
Deprecated/MGN9H/Electronics/M5P_Box.stl
Deprecated/MGN9H/Electronics/M5P_Cover_4010.stl
Deprecated/MGN9H/Electronics/TFT35SPI_Cover.stl
Deprecated/MGN9H/Electronics/TFT35SPI_Housing.stl
Deprecated/MGN9H/Extras/97mm_spacing_jig.stl
Deprecated/MGN9H/Extras/Brush_Hold.stl
Deprecated/MGN9H/Extras/Camera_Mount_1.stl
Deprecated/MGN9H/Extras/Camera_Mount_2.stl
Deprecated/MGN9H/Extras/Purge_Bucket.stl
Deprecated/MGN9H/Extras/Purge_Slope.stl
Deprecated/MGN9H/Extras/Y_rails_stopper.stl
Deprecated/MGN9H/X Axis/Y_Carriage_Bottom_Left.stl
Deprecated/MGN9H/X Axis/Y_Carriage_Bottom_Right.stl
Deprecated/MGN9H/X Axis/Y_Carriage_Top_Left.stl
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

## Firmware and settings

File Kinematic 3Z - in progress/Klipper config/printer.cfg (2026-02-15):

# This file contains common pin mappings for the BigTreeTech E3 RRF 1.1.
# To use this config, the firmware should be compiled for the
# STM32F407 with a "32KiB bootloader".

# The "make flash" command does not work on the E3 RRF 1.1. Instead,
# after running "make", copy the generated "out/klipper.bin" file to a
# file named "firmware.bin" on an SD card and then restart the E3 RRF
# 1.1 with that SD card.

# See docs/Config_Reference.md for a description of parameters.

[include mainsail.cfg]
[include display.cfg]
[include menu.cfg]
[include timelapse.cfg]
[include Adaptive_Mesh.cfg]
[include Line_Purge.cfg]
[include macros.cfg]
[include sensorless.cfg]



[exclude_object]
  
[gcode_arcs]
resolution: 0.1

[mcu]
serial: /dev/serial/by-id/usb-Klipper_stm32f407xx_300021001047303033333839-if00

[printer]
kinematics: corexy
minimum_cruise_ratio: 0
max_velocity: 500
max_accel: 20000
max_z_velocity: 50
max_z_accel: 250

[extruder]
step_pin: PD12
dir_pin: PD13
enable_pin: !PD10
microsteps: 32
rotation_distance: 3.45
pressure_advance: 0.024
nozzle_diameter: 0.600
filament_diameter: 1.750
heater_pin: PB3
sensor_type: ATC Semitec 104GT-2
sensor_pin: PA0
control: pid
pid_Kp = 40.185
pid_Ki = 12.757
pid_Kd = 31.646
min_temp: 0
max_temp: 280
max_extrude_cross_section: 9999999
max_extrude_only_distance: 700
min_extrude_temp: 0

[tmc2209 extruder]
uart_pin: PD11
run_current: 0.850
hold_current: 0.500
diag_pin: ^PC3    # Set to MCU pin connected to TMC DIAG pin
driver_SGTHRS: 255 # 255 is most sensitive value, 0 is least sensitive

[bltouch]
sensor_pin: ^PC5
control_pin: PB0
x_offset: -34.1
y_offset: -11.7
#Higher the offset, the closer to the bed the nozzle will be.
#Lower the offset, the further the nozzle will be.
#If you need more squish or if it's too high, increase the offset.
#If it's too close, lower the offset.
z_offset = 0.55
#pin_move_time: 0.8
probe_with_touch_mode: True
pin_up_touch_mode_reports_triggered: False
stow_on_each_sample: False

[bed_mesh]
speed: 150
horizontal_move_z: 7
mesh_min: 20,20
mesh_max: 195, 210
probe_count: 5,5
algorithm: lagrange
fade_start: 1
fade_end: 10
#fade_target: 0
bicubic_tension: 0.15


[thermistor NTC100K-B3950]
temperature1: 25
resistance1: 100000
temperature2: 160
resistance2: 1374
temperature3: 300
resistance3: 84.78


[adxl345]
cs_pin: rpi:gpio74
spi_bus: spidev1.1

[resonance_tester]
accel_chip: adxl345
probe_points:
  110, 115, 30
#sweeping_period: 0


[input_shaper]
shaper_type_x: mzv
shaper_freq_x: 66.6
shaper_type_y: mzv
shaper_freq_y: 54.8


[stepper_x]
step_pin: PD0
dir_pin: PA15
enable_pin: !PD3
microsteps: 32
rotation_distance: 39.8
#rotation_distance: 40
endstop_pin: tmc2209_stepper_x:virtual_endstop
position_min: -2
position_endstop: -2
position_max: 230
homing_speed: 50
homing_retract_dist: 0

[tmc2209 stepper_x]
uart_pin: PD6
run_current: 0.900
hold_current: 0.700
diag_pin: ^PC0     # Set to MCU pin connected to TMC DIAG pin
driver_SGTHRS: 120 # 255 is most sensitive value, 0 is least sensitive
interpolate: False

[stepper_y]
step_pin: PD5
dir_pin: PD4
enable_pin: !PD7
microsteps: 32
rotation_distance: 39.8
#rotation_distance: 40
endstop_pin: tmc2209_stepper_y:virtual_endstop
#endstop_pin: !PC1
position_min: -17
position_endstop: 250
position_max: 250
homing_speed: 40
homing_retract_dist: 0

[tmc2209 stepper_y]
uart_pin: PD1
run_current: 0.900
hold_current: 0.700
diag_pin: ^PC1      # Set to MCU pin connected to TMC DIAG pin
driver_SGTHRS: 90 #115 # 255 is most sensitive value, 0 is least sensitive
interpolate: False

[stepper_z]
step_pin: PC6
dir_pin: !PC7
enable_pin: !PD14
microsteps: 32
rotation_distance: 8
#endstop_pin: tmc2209_stepper_z:virtual_endstop
endstop_pin: probe:z_virtual_endstop
#position_endstop: 0
position_max: 270
position_min: -1
homing_speed: 25
homing_retract_dist: 0

[tmc2209 stepper_z]
uart_pin: PD15
run_current: 0.900

#diag_pin: ^PC2     # Set to MCU pin connected to TMC DIAG pin
#driver_SGTHRS: 5  # 255 is most sensitive value, 0 is least sensitive


[verify_heater extruder]
check_gain_time: 20
#   This controls heater verification during initial heating. Smaller
#   values result in stricter checking and larger values allow for
#   more time before an error is reported. Specifically, during
#   initial heating, as long as the heater increases in temperature
#   within this time frame (specified in seconds) then the internal
#   "error counter" is reset. The default is 20 seconds for extruders
#   and 60 seconds for heater_bed.
hysteresis: 10
#   The maximum temperature difference (in Celsius) to a target
#   temperature that is considered in range of the target. This
#   controls the max_error range check. It is rare to customize this
#   value. The default is 5.
heating_gain: 2
#   The minimum temperature (in Celsius) that the heater must increase
#   by during the check_gain_time check. It is rare to customize this
#   value. The default is 2.



[heater_bed]
heater_pin: PB4
sensor_type: EPCOS 100K B57560G104F
sensor_pin: PA1
control: pid
pid_Kp = 75.448
pid_Ki = 1.935
pid_Kd = 735.620
min_temp: 0
max_temp: 130

[heater_fan heatbreak_cooling_fan]
pin: PB6

[fan]
pin: PB5

[temperature_sensor MCU] 
sensor_type: temperature_mcu

[temperature_sensor CB1] 
sensor_type: temperature_host

[bed_screws]
screw1: 30.5, 37
screw2: 30.5, 207
screw3: 204.5, 207
screw4: 204.5, 37

# Warning: display section not tested!

[board_pins]
aliases:
    # EXP1 header
    EXP1_1=PE8, EXP1_3=PE7,   EXP1_5=PB2,  EXP1_7=PB1,  EXP1_9=<GND>,
    EXP1_2=PE9, EXP1_4=<RST>, EXP1_6=PE10, EXP1_8=PE11, EXP1_10=<5V>

[display]
lcd_type: st7920
cs_pin: EXP1_7
sclk_pin: EXP1_6
sid_pin: EXP1_8
encoder_pins: ^EXP1_5, ^EXP1_3
click_pin: ^!EXP1_2

[output_pin beeper]
pin: EXP1_1

[mcu rpi]
serial: /tmp/klipper_host_mcu




# See the sample-lcd.cfg file for definitions of common LCD displays.

#*# <---------------------- SAVE_CONFIG ---------------------->
#*# DO NOT EDIT THIS BLOCK OR BELOW. The contents are auto-generated.
#*#
#*# [extruder]
#*#
#*# [bed_mesh 60]
#*# version = 1
#*# points =
#*# 	0.111250, 0.186250, 0.181875, 0.156250, 0.118750
#*# 	0.109375, 0.184375, 0.149375, 0.082500, 0.016875
#*# 	0.115625, 0.166875, 0.135000, 0.110000, 0.031875
#*# 	0.065000, 0.161250, 0.154375, 0.118750, 0.052500
#*# 	0.146250, 0.261875, 0.265625, 0.210000, 0.130000
#*# x_count = 5
#*# y_count = 5
#*# mesh_x_pps = 2
#*# mesh_y_pps = 2
#*# algo = lagrange
#*# tension = 0.2
#*# min_x = 20.0
#*# max_x = 214.0
#*# min_y = 20.0
#*# max_y = 190.0
#*#
#*# [bed_mesh default]
#*# version = 1
#*# points =
#*# 	  -0.012500, 0.076875, 0.051875, -0.038125, -0.140625
#*# 	  0.020625, 0.105000, 0.064375, 0.015000, -0.121250
#*# 	  0.008125, 0.103125, 0.052500, 0.006875, -0.110625
#*# 	  0.005625, 0.133750, 0.094375, 0.067500, -0.048125
#*# x_count = 5
#*# y_count = 4
#*# mesh_x_pps = 2
#*# mesh_y_pps = 2
#*# algo = lagrange
#*# tension = 0.2
#*# min_x = 31.22
#*# max_x = 200.81
#*# min_y = 53.51
#*# max_y = 178.1

#[stallguardextras]

#[collision_detection]
#update_time: 0.01       # time in seconds to query the drivers
#deviation_tolerance: 50
# sgthrs: 250
# sgt: 0 #

#[extruder_detection]
#WIP

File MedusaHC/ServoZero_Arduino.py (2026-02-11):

///////////////////////////////////////////////////////////////////////////////////////////////////////////////////////////////
//         Arduino code for setting servo (Hi-Tech 311) to the neutral position
//         See the following video on my channel "Let There Be Engineering" for more details:
//         https://youtu.be/9Hul2amhBSM "How to Set a Servo Motor to the Neutral Position using Arduino: A Step-by-Step Guide" 
/////////////////////////////////////////////////////////////////////////////////////////////////////////////////////////////////

#include <Servo.h>

int pos;  // position of servo (range between 0 and 180; 90 is the neutral position) 
int servoPin=9; // analog 9 pin for servo
int servoDelay = 2000;  // Delay servo by 2 seconds 

Servo myTestSubject;  // Declare servo object

void setup() {
Serial.begin(9600);
myTestSubject.attach(servoPin);
    pos=0;  // Move servo to position 0 = minimum position
    myTestSubject.write(pos);
    Serial.println(pos);  // Display position 
    delay(servoDelay);

    pos=90;  // Move servo to position 90 = middle position
    myTestSubject.write(pos);
    Serial.println(pos);  // Display position 
    delay(servoDelay);

    pos=180;  // Move servo to position 180 = maximum position
    myTestSubject.write(pos);
    Serial.println(pos);  // Display position 
    delay(servoDelay);

    pos=90;  // Move servo to position 0 = min position (zero as MedusaHC script)
    myTestSubject.write(pos);
    Serial.println(pos);  // Display position 
    delay(servoDelay);
}

void loop() {

}

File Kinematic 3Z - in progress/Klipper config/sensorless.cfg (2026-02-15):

##Taken from here: https://github.com/EricZimmerman/Voron02/blob/master/macros/helpers/homing.cfg

#required for SET_KINEMATIC_POSITION to work.

[force_move]
enable_force_move: true

[gcode_macro _HOME_X]
gcode:
    # Always use consistent run_current on A/B steppers during sensorless homing
    {% set RUN_CURRENT_X = printer.configfile.settings['tmc2209 stepper_x'].run_current|float %}
    {% set RUN_CURRENT_Y = printer.configfile.settings['tmc2209 stepper_y'].run_current|float %}
    {% set HOME_CURRENT = 0.7 %}
    SET_TMC_CURRENT STEPPER=stepper_x CURRENT={HOME_CURRENT}
    SET_TMC_CURRENT STEPPER=stepper_y CURRENT={HOME_CURRENT}

    # Home
    G28 X
    # Move away
    G91
    G1 X10 F4000
    
    # Wait just a second (give StallGuard registers time to clear)
    G4 P500

    # Set current during print
    SET_TMC_CURRENT STEPPER=stepper_x CURRENT={RUN_CURRENT_X}
    SET_TMC_CURRENT STEPPER=stepper_y CURRENT={RUN_CURRENT_Y}

[gcode_macro _HOME_Y]
gcode:
    # Set current for sensorless homing
    {% set RUN_CURRENT_X = printer.configfile.settings['tmc2209 stepper_x'].run_current|float %}
    {% set RUN_CURRENT_Y = printer.configfile.settings['tmc2209 stepper_y'].run_current|float %}
    {% set HOME_CURRENT = 0.7 %}
    SET_TMC_CURRENT STEPPER=stepper_x CURRENT={HOME_CURRENT}
    SET_TMC_CURRENT STEPPER=stepper_y CURRENT={HOME_CURRENT}

    # Home
    G28 Y
    # Move away
    G91
    G1 Y-10 F4000

    # Wait just a second (give StallGuard registers time to clear)
    G4 P500
    
    # Set current during print
    SET_TMC_CURRENT STEPPER=stepper_x CURRENT={RUN_CURRENT_X}
    SET_TMC_CURRENT STEPPER=stepper_y CURRENT={RUN_CURRENT_Y}

[gcode_macro _HOME_Z]
gcode:
    G90
    G1 X125 Y125 F6000
    G28 Z
    G1 Z15
    
[homing_override]
axes: xyz
gcode:
  {% set home_all = 'X' not in params and 'Y' not in params and 'Z' not in params %}

  SET_KINEMATIC_POSITION Z=1
  G1 Z15 F1200

  {% if home_all or 'X' in params %}
    _HOME_X
  {% endif %}
  
  {% if home_all or 'Y' in params %}
    _HOME_Y
  {% endif %}

  {% if home_all or 'Z' in params %}
    _HOME_Z
  {% endif %}

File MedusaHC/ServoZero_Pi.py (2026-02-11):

# Import libraries
import RPi.GPIO as GPIO
import time

# Set GPIO numbering mode
GPIO.setmode(GPIO.BOARD)

# Set pin 11 as an output, and set servo1 as pin 11 as PWM
GPIO.setup(11,GPIO.OUT)
servo1 = GPIO.PWM(11,50) # Note 11 is pin, 50 = 50Hz pulse

#start PWM running, but with value of 0 (pulse off)
servo1.start(0)
print ("Waiting for 2 seconds")
time.sleep(2)

#Let's move the servo!
print ("Rotating 180 degrees in 10 steps")

# Define variable duty
duty = 2

# Loop for duty values from 2 to 12 (0 to 180 degrees)
print ("Testing servo full course")
while duty <= 12:
    servo1.ChangeDutyCycle(duty)
    time.sleep(1)
    duty = duty + 1

# Wait a couple of seconds
time.sleep(2)

# Turn back to 90 degrees
print ("Zeroing back to 0 degrees")
servo1.ChangeDutyCycle(2)
time.sleep(0.5)
servo1.ChangeDutyCycle(0)

#Clean things up at the end
servo1.stop()
GPIO.cleanup()
print ("Done! Byebye.")

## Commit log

2026-01-29 Corrected AB_right_motor_mount.stl
    [AB_right_motor_mount.stl]
2026-02-11 Added deprecated versions
    [97mm_spacing_jig.stl, AB_Front_Hold_Left.stl, AB_Front_Hold_Right.stl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]
2026-02-14 Added AdaptedAdapter STL
    [AdaptedAdapter_1.5mm.stl, AdaptedAdapter_1mm.stl, AdaptedAdapter_2mm.stl]
2026-02-15 Update 3Z
    [2020_Cable_Mount_x1.stl, 2040_Cam_Lid_x1.stl, 2040_Half_Lid_x3.stl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]
2026-02-16 Duender v6Pins upload
    [Dragonburner_Cowl.stl, Dragonburner_SherpaMini_Mount.stl, Dragonburner_X1_Mount.stl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]
2026-02-16 Update AB Motor mounts
    [AB_Motor_Bottom_Left.stl, AB_Motor_Bottom_Right.stl]
2026-02-17 Corrected MGN1H toolhead carriage
    [[12H]_Carriage_Mount.stl]
2026-02-20 Added Extras to Pins version
    [Duender_Logo.stl, Extra_Mount_Left.stl, Extra_Mount_Right.stl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]
2026-02-21 Replaced TFT35 by HDMI5
    [HDMI5_Frame.stl, HDMI5_Mount_noLogo.stl, HDMI5_Mount_wLogo.stl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]
2026-03-16 Update Bed kinematic parts
    [Bed_holder_Back.stl, Bed_holder_Left.stl, Bed_holder_Right.stl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]
